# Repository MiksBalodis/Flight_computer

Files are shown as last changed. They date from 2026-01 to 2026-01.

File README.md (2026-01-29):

# Aktīvās kontroles raķetes avionikas sistēma

## Projekta apraksts
Šis projekts paredz aktīvās kontroles raķetes avionikas sistēmas izstrādi, kas ietver gan raķetē iebūvētu avionikas datoru, gan zemes bāzi datu saņemšanai, uzglabāšanai un analīzei. Sistēma nodrošina aktīvu trajektorijas korekciju reāllaikā, izmantojot sensoru datus, vadības algoritmus un elektroniskos izpildmehānismus.

Projektā tiek apvienotas iegultās sistēmas, signālu apstrāde, vadības algoritmi, telemetrija un lietotāja saskarnes izstrāde.

**Projektu izstrādā:**  
Aleksandrs Jesiļevskis  
Miks Balodis  

---

## Projekta mērķis
Izstrādāt:
- raķetes avionikas datoru ar aktīvas trajektorijas korekcijas iespējām,
- zemes bāzi lidojuma datu saņemšanai un analīzei,
- drošu un papildināmu sistēmu, kas piemērota eksperimentālām lieljaudas raķetēm.

Sistēmai jāspēj:
- reāllaikā noteikt raķetes stāvokli,
- veikt aktīvo vadību ar vairākām kontroles spurām,
- ierakstīt un uzglabāt lidojuma datus,
- nodrošināt saziņu ar zemes bāzi lidojuma laikā.

---

## Idejas rašanās
Ideja radās, balstoties uz **RTU Lieljaudas raķeškomandas (RTU HPR)** 2025. gada 1. semestra projektu – aktīvās rotācijas kontroles raķeti. Šī projekta ietvaros tika izmantots RP2040 mikrokontrolieris, kuram konstatēti vairāki ierobežojumi:
- nav iebūvēta peldošā komata vienības (FPU),
- ierobežota programmas atmiņa,
- augsts enerģijas patēriņš.

Lai šos trūkumus novērstu, projektā tiek izvēlēts **STM32F405RGT6**, kas nodrošina augstāku veiktspēju, FPU atbalstu un DSP instrukcijas.

---

## Idejas apraksts

### Projekta lietotāji
- studentu raķešu komandas,
- augstskolu/vidusskolu eksperimentēšanas grupas,
- iegulto sistēmu un vadības algoritmu izstrādātāji,
- eksperimentālu raķešu un bezpilota sistēmu entuziasti.

### Izmantotās tehnoloģijas
- **Iegultās sistēmas:** STM32 (ARM Cortex-M4)
- **Sensori:** barometrs, IMU, GNSS
- **Vadības algoritmi:** PID, Kalmana filtrs
- **Telemetrija:** sub-GHz radio sakari
- **Programmatūra:** C/C++, MatLab/Simulink (simulācijas), JavaScript un Svelte (GUI)
- **Projektēšana:** KiCad

### Piegādes formāts
Projekta rezultāts būs:
- raķetes avionikas sistēmas plate (PCB),
- iegultā programmatūra gatava demonstratīvam raķetes lidojumam (firmware),
- zemes bāzes programmatūra (GUI),
- dokumentācija.

Šāda pieeja ļauj sistēmu izmantot gan eksperimentālos lidojumos, gan simulācijās.

---

## Aktīvā kontrole
Aktīvā kontrole ir vadības sistēma, kas lidojuma laikā nepārtraukti:
- mēra raķetes stāvokli (leņķi, ātrumu, rotāciju),
- aprēķina nepieciešamos labojumus,
- ģenerē PWM signālus izpildmehānismiem servo kontrolētām spurām.

Sistēma atbalsta līdz **4 aktīvām spurām**, katrai paredzot atsevišķu PWM kanālu. Salīdzinājumā ar pasīvo kontroli, aktīvā kontrole spēj reaģēt uz ārējiem traucējumiem un uzlabot stabilitāti un precizitāti.

---

## Risinājuma arhitektūra

### Konceptuālais modelis
Sistēma sastāv no trim galvenajiem blokiem:
1. **Sensoru slānis** – datu iegūšana
2. **Vadības un apstrādes slānis** – aprēķini un lēmumu pieņemšana
3. **Izpildes un komunikācijas slānis** – kontrole, datu uzglabāšana un pārraide

### Tehniskā arhitektūra

#### MCU
- **STM32F405RGT6** - mikrokontrolieris datu apstrādei un komandu nodošanai

#### Sensori
- **BMP388** – barometrs augstuma noteikšanai
- **LSM6DSO** – IMU (akselerometrs + žiroskops)
- **MAX-M10S** – GNSS modulis augstas precizitātes pozīcijai

#### Datu uzglabāšana
- **MXL1606** – lidojuma datu ierakstīšanai (USB Mass Storage režīms)
- **24LC64 EEPROM** – konfigurācijas datiem

#### Telemetrija
- **EBYTE E22-400M22S** - LoRa moudlis saziņai ar zemes bāzi (433 MHz)

#### Vadība
- PWM signāli spuru servo
- PID regulators
- Kalmana filtrs stāvokļa novērtēšanai

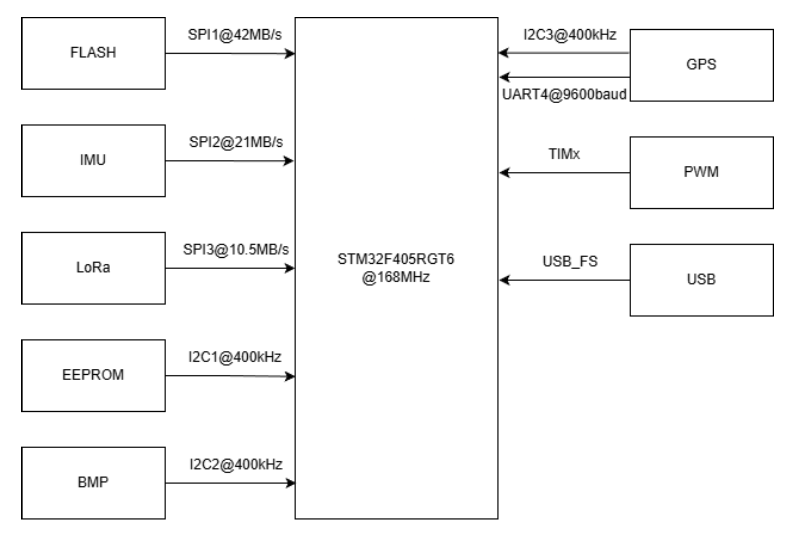
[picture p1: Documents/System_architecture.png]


---
## Izstrādes plāns (10 nedēļas)

Projekta izstrāde ir plānota 10 nedēļu laikā, pieņemot, ka avionikas plate jau ir uzdizainēta un pasūtīta, un nākamais solis ir tās salodēšana. Darbs tiek sadalīts starp diviem izstrādātājiem, lai maksimāli efektīvi izmantotu paralēlu izstrādi.

### Lomu sadalījums
- **Aleksandrs** – iegultās sistēmas programmēšana, STM32 firmware, sensoru draiveri, datu plūsma, vadība un telemetrija, sistēmas arhitektūras lēmumi,  integrācija, testēšana un dokumentācija.
- **Miks** – raķetes tehniskā daļa, mehāniskā integrācija, Matlab/Simulink simulācijas, vadības algoritmu modelēšana un zemes stacijas aparatūra, sistēmas arhitektūras lēmumi,  integrācija, testēšana un dokumentācija.

---

### 1. nedēļa – Sistēmas inicializācija un modeļu sagatavošana
**Aleksandrs:**
- STM32CubeIDE projekta izveide
- Pulksteņu (clock tree) un pamata perifēriju konfigurācija
- Debug interfeisa (SWD/UART) inicializācija

**Miks:**
- Raķetes kustības konceptuālā modeļa izstrāde
- Aktīvās kontroles uzdevuma definēšana
- Sensoru mērījumu teorētisko modeļu izveide

**Rezultāts:**  
MCU veiksmīgi startē un sistēmas matemātiskais modelis ir definēts.

---

### 2. nedēļa – Perifēriju un datu plūsmas pamati
**Aleksandrs:**
- GPIO, UART, SPI un I2C konfigurācija
- DMA izmantošanas pamati datu pārsūtīšanai
- Vienkārša datu izvada testēšana

**Miks:**
- PID regulatora struktūras izveide Matlab/Simulink
- Sākotnējo vadības parametru novērtēšana
- Avionikas plates salodēšana

**Rezultāts:**  
MCU spēj komunicēt ar perifērijām, un PID struktūra ir gatava simulācijām, plate ir salodēta.

---

### 3. nedēļa – Avionikas plates salodēšana un sensoru testēšana
**Aleksandrs:**
- IMU (LSM6DSO) un barometra (BMP388) draiveru izstrāde
- Sensoru datu nolasīšana un izvadīšana caur UART

**Miks:**
- Barošanas un signālu līmeņu pārbaude
- Sensoru fiziskās integrācijas novērtēšana

**Rezultāts:**  
Pilnībā funkcionējoši aktīvie sensori.

---

### 4. nedēļa – GNSS un sensoru apvienošana
**Aleksandrs:**
- GNSS (MAX-M10S) draivera izstrāde
- Laika sinhronizācija starp sensoriem
- Datu struktūru definēšana

**Miks:**
- Sensoru kalibrācijas metodes
- Kļūdu modelēšana
- Mērījumu precizitātes izvērtēšana

**Rezultāts:**  
Apvienoti visi sensoru dati vienotā laika skalā.

---

### 5. nedēļa – Aktīvā vadība un izpildmehānismi
**Aleksandrs:**
- PWM izvades konfigurācija
- Taimeru konfigurācija izpildmehānismiem
- Izpildmehānismu testēšana

**Miks:**
- PID parametru regulēšana Simulink vidē
- Stabilitātes analīze
- Vadības algoritma validācija simulācijā

**Rezultāts:**  
Izpildmehānismi reaģē uz vadības signāliem paredzētajā veidā.

---

### 6. nedēļa – Datu apstrāde un uzglabāšana
**Aleksandrs:**
- USB Mass Storage režīma ieviešana
- Datu struktūras optimizācija

**Miks:**
- Kalmana filtra izstrāde Simulink vidē
- Algoritma sagatavošana ieviešanai C kodā

**Rezultāts:**  
Stabili ierakstīti un izgūstami lidojuma dati.

---

### 7. nedēļa – Telemetrija un zemes stacijas aparatūra
**Aleksandrs:**
- Telemetrijas protokola izstrāde
- EBYTE E22 radio moduļa integrācija
- Datu pakešu formāta definēšana

**Miks:**
- Zemes stacijas plates arhitektūras izstrāde
- Komponentu izvēle un shēmas dizains
- Komunikācijas interfeisa plānošana

**Rezultāts:**  
Bezvadu datu pārraide starp raķeti un zemes staciju.

---

### 8. nedēļa – Zemes stacijas programmatūra un GUI
**Aleksandrs:**
- Seriālās komunikācijas protokols ar datoru
- Telemetrijas datu parsēšana

**Miks:**
- Grafiskās lietotāja saskarnes izstrāde (Svelte)
- Reāllaika grafiki un datu attēlošana
- Datu eksportēšana analīzei

**Rezultāts:**  
Darbojoša zemes stacija ar reāllaika datu vizualizāciju.

---

### 9. nedēļa – Integrācija un sistēmas testi
**Aleksandrs:**
- Pilna vadības cikla integrācija
- Kļūdu apstrāde un drošības mehānismi

**Miks:**
- Vibrāciju testi
- Sensoru trokšņu ietekmes pārbaude

**Rezultāts:**  
Stabila un integrēta sistēma bez kritiskām kļūdām.

---

### 10. nedēļa – Stabilizācija un dokumentācija
**Abi:**
- Koda un aparatūras kļūdu labošana
- Projekta dokumentācijas pabeigšana
- Demonstrācijas sagatavošana

**Rezultāts:**  
Pilnībā sagatavots projekts demonstrācijai un prezentācijai.

---

## Projekta izstrādes grafiks

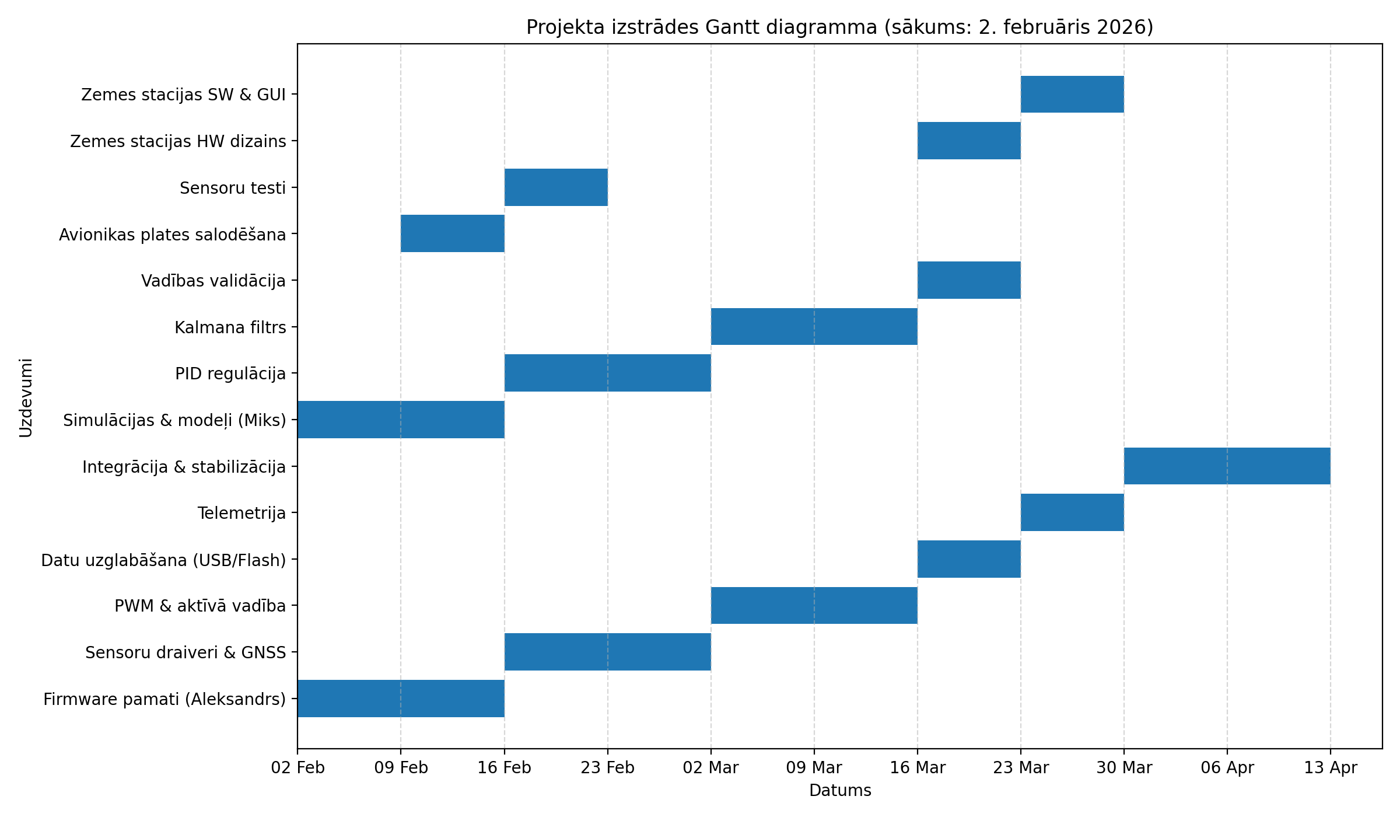
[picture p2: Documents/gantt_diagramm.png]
Projekta izstrādes Gantt diagramma


---

## Licence
Licence tiks noteikta projekta vēlākā izstrādes posmā.

---

## Kontakti
Jautājumu vai sadarbības gadījumā sazināties ar projekta izstrādātājiem.

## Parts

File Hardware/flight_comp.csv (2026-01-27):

Reference | Qty | Value | DNP | Exclude from BOM | Exclude from Board | Footprint | Datasheet
BT1 | 1 | MC621 |  |  |  | Battery:BatteryHolder_Keystone_2998_1x6.8mm | ~
BZ1 | 1 | Buzzer |  |  |  | Buzzer_Beeper:Buzzer_CUI_CPT-9019S-SMT | ~
C1,C2,C3,C34,C37,C41 | 6 | 100nF |  |  |  | Capacitor_SMD:C_0402_1005Metric | ~
C4 | 1 | 10µF |  |  |  | Capacitor_SMD:C_0402_1005Metric | ~
C5 | 1 | 47 µF |  |  |  | Capacitor_SMD:C_1206_3216Metric | ~
C6,C7 | 2 | 2.2uF |  |  |  | Capacitor_SMD:C_0603_1608Metric | ~
C8,C9 | 2 | 22pF |  |  |  | Capacitor_SMD:C_0603_1608Metric | ~
C10,C11,C14,C26,C27,C28,C29,C30,C31,C32,C33 | 11 | 0.1uF |  |  |  | Capacitor_SMD:C_0603_1608Metric | ~
C12 | 1 | 6.8nF |  |  |  | Capacitor_SMD:C_0603_1608Metric | ~
C13 | 1 | 1uF |  |  |  | Capacitor_SMD:C_0603_1608Metric | ~
C15 | 1 | 44uF |  |  |  | Capacitor_SMD:C_0805_2012Metric | ~
C16 | 1 | 22uF |  |  |  | Capacitor_SMD:C_0805_2012Metric | ~
C17 | 1 | 100nF |  |  |  | Capacitor_SMD:C_0603_1608Metric | ~
C18,C42 | 2 | 10uF |  |  |  | Capacitor_SMD:C_0603_1608Metric | ~
C19 | 1 | 22uF |  |  |  | Capacitor_SMD:C_0603_1608Metric | ~
C20,C23 | 2 | 22pF |  |  |  | Capacitor_SMD:C_0402_1005Metric | ~
C21,C22 | 2 | 0.1uF |  |  |  | Capacitor_SMD:C_0402_1005Metric | ~
C24 | 1 | 6TPF470MFH |  |  |  | Capacitor_Tantalum_SMD:CP_EIA-3216-10_Kemet-I | https://industrial.panasonic.com/cdbs/www-data/pdf/AAA8000/AAA8000C38.pdf
C35,C36 | 2 | 10uF |  |  |  | Capacitor_SMD:C_0402_1005Metric | ~
D1 | 1 | LED |  |  |  | LED_SMD:LED_0603_1608Metric | ~
D2,D5 | 2 | D_TVS |  |  |  | Diode_SMD:D_SOD-523 | ~
D3 | 1 | SS24 |  |  |  | Diode_SMD:D_SMA | https://www.vishay.com/docs/88748/ss22.pdf
D4 | 1 | SK6812 |  |  |  | LED_SMD:LED_SK6812_PLCC4_5.0x5.0mm_P3.2mm | https://cdn-shop.adafruit.com/product-files/1138/SK6812+LED+datasheet+.pdf
D6 | 1 | 3.6V |  |  |  | Diode_SMD:D_SOD-128 | ~
E22-400M22S2 | 1 | ~ |  |  |  | E22-400M22S:E22-400M22S
F1 | 1 | Fuse |  |  |  | Fuse:Fuse_1206_3216Metric | ~
H1,H2,H3,H4 | 4 | MountingHole |  | Excluded from BOM |  | MountingHole:MountingHole_3.2mm_M3 | ~
IC1 | 1 | BMP388 |  |  |  | Package_LGA:ST_HLGA-10_2x2mm_P0.5mm_LayoutBorder3x2y | https://ae-bst.resource.bosch.com/media/_tech/media/datasheets/BST-BMP388-DS001.pdf
IC4 | 1 | TPS259531DSGR |  |  |  | Package_SON:WSON-8-1EP_2x2mm_P0.5mm_EP0.9x1.6mm_ThermalVias | http://www.ti.com/lit/gpn/tps2595
J1,J12 | 2 | Conn_Coaxial |  |  |  | Connector_Coaxial:SMA_Molex_73251-2200_Horizontal | ~
J2 | 1 | TC2030 |  | Excluded from BOM |  | Connector:Tag-Connect_TC2030-IDC-NL_2x03_P1.27mm_Vertical | https://www.tag-connect.com/wp-content/uploads/bsk-pdf-manager/2019/12/TC2030-IDC-NL-Datasheet-Rev-B.pdf
J3 | 1 | XT30 |  |  |  | Connector_AMASS:AMASS_XT30PW-M_1x02_P2.50mm_Horizontal | ~
J4 | 1 | USB_C_Receptacle_USB2.0_16P |  |  |  | Connector_USB:USB_C_Receptacle_GCT_USB4110 | https://www.usb.org/sites/default/files/documents/usb_type-c.zip
J5,J6 | 2 | Conn_01x02 |  |  |  | TerminalBlock_4Ucon:TerminalBlock_4Ucon_1x02_P3.50mm_Vertical | ~
J7 | 1 | SERVO_CONN_01 |  |  |  | Connector_PinHeader_2.54mm:PinHeader_2x03_P2.54mm_Vertical | ~
J8,J9 | 2 | SERVO_CONN_02 |  |  |  | Connector_PinHeader_2.54mm:PinHeader_2x03_P2.54mm_Vertical | ~
J10 | 1 | CAMERA_CONN_01 |  |  |  | TerminalBlock:TerminalBlock_Xinya_XY308-2.54-2P_1x02_P2.54mm_Horizontal | ~
J11 | 1 | CAMERA_CONN_02 |  |  |  | TerminalBlock:TerminalBlock_Xinya_XY308-2.54-2P_1x02_P2.54mm_Horizontal | ~
J13 | 1 | CAMERA_CONN_03 |  |  |  | TerminalBlock:TerminalBlock_Xinya_XY308-2.54-2P_1x02_P2.54mm_Horizontal | ~
L1 | 1 | 2.2uH |  |  |  | Inductor_SMD:L_6.3x6.3_H3 | ~
L2 | 1 | L |  |  |  | Inductor_SMD:L_0603_1608Metric | ~
Q2 | 1 | DMP3013SFV |  |  |  | Package_SON:Diodes_PowerDI3333-8 | https://www.diodes.com/assets/Datasheets/DMP3013SFV.pdf
Q3,Q4 | 2 | CSD17577Q3A |  |  |  | Package_SON:VSON-8_3.3x3.3mm_P0.65mm_NexFET | https://www.ti.com/lit/ds/symlink/csd17577q3a.pdf
Q5 | 1 | PMBT2222A |  |  |  | Package_TO_SOT_SMD:SOT-23 | https://assets.nexperia.com/documents/data-sheet/PMBT2222A.pdf
R1,R2,R3,R4 | 4 | 100Ω |  |  |  | Resistor_SMD:R_0402_1005Metric | ~
R5,R6,R7,R21 | 4 | 10k |  |  |  | Resistor_SMD:R_0603_1608Metric | ~
R8,R33 | 2 | 1k |  |  |  | Resistor_SMD:R_0603_1608Metric | ~
R9 | 1 | 604k |  |  |  | Resistor_SMD:R_0603_1608Metric | ~
R10 | 1 | 40.2k |  |  |  | Resistor_SMD:R_0603_1608Metric | ~
R11 | 1 | 13k |  |  |  | Resistor_SMD:R_0603_1608Metric | ~
R12 | 1 | 20k |  |  |  | Resistor_SMD:R_0603_1608Metric | ~
R13 | 1 | 20R |  |  |  | Resistor_SMD:R_0603_1608Metric | ~
R14 | 1 | 4.7k |  |  |  | Resistor_SMD:R_0603_1608Metric | ~
R15,R16 | 2 | 22R |  |  |  | Resistor_SMD:R_0603_1608Metric | ~
R17,R18,R19,R20,R22,R23 | 6 | 100 |  |  |  | Resistor_SMD:R_0402_1005Metric | ~
R24,R25,R26,R27,R28,R29 | 6 | R | DNP |  |  | Resistor_SMD:R_0603_1608Metric | ~
R30,R31 | 2 | R |  |  |  | Resistor_SMD:R_0603_1608Metric | ~
R32 | 1 | 0R | DNP |  |  | Resistor_SMD:R_0603_1608Metric | ~
R34 | 1 | 5k |  |  |  | Resistor_SMD:R_0402_1005Metric | ~
R48 | 1 | 220Ω |  |  |  | Resistor_SMD:R_0402_1005Metric | ~
SW1 | 1 | NRST |  |  |  | Button_Switch_SMD:SW_SPST_CK_RS282G05A3 | ~
SW2 | 1 | BOOT0 |  |  |  | Button_Switch_SMD:SW_SPST_CK_RS282G05A3 | ~
SW3 | 1 | EG2219 |  |  |  | Button_Switch_SMD:SW_DPDT_CK_JS202011JCQN | ~
TX4 | 1 | XL-1608UBC-04 |  |  |  | LED_SMD:LED_0603_1608Metric | https://fscdn.rohm.com/en/products/databook/datasheet/discrete/diode/switching/1ss355vmte-17-e.pdf
U1 | 1 | STM32F405RGTx |  |  |  | Package_QFP:LQFP-64_10x10mm_P0.5mm | https://www.st.com/resource/en/datasheet/stm32f405rg.pdf
U2 | 1 | MAX-M10S |  |  |  | RF_GPS:ublox_MAX | https://content.u-blox.com/sites/default/files/MAX-M10S_DataSheet_UBX-20035208.pdf
U3 | 1 | 74LVC1GU04 |  |  |  | Package_TO_SOT_SMD:SOT-23-5 | http://www.ti.com/lit/sg/scyt129e/scyt129e.pdf
U4 | 1 | W25Q32JVSS |  |  |  | Package_SO:SOIC-8_5.3x5.3mm_P1.27mm | http://www.winbond.com/resource-files/w25q32jv%20revg%2003272018%20plus.pdf
U5 | 1 | 24LC64 |  |  |  | Package_TO_SOT_SMD:SOT-23-5 | http://ww1.microchip.com/downloads/en/DeviceDoc/21189f.pdf
U6 | 1 | MP2331 |  |  |  | Package_TO_SOT_SMD:SOT-583-8
U7 | 1 | AMS1117-5.0 |  |  |  | Package_TO_SOT_SMD:SOT-223-3_TabPin2 | http://www.advanced-monolithic.com/pdf/ds1117.pdf
U8 | 1 | USBLC6-2SC6 |  |  |  | Package_TO_SOT_SMD:SOT-23-6 | https://www.st.com/resource/en/datasheet/usblc6-2.pdf
U10 | 1 | LTC4412 |  |  |  | Package_TO_SOT_SMD:TSOT-23-6 | https://www.analog.com/media/en/technical-documentation/data-sheets/4412fb.pdf
U11,U12 | 2 | UCC27517A |  |  |  | Package_TO_SOT_SMD:SOT-23-5 | https://www.ti.com/lit/ds/symlink/ucc27517a.pdf
U13 | 1 | LSM6DSO |  |  |  | Package_LGA:LGA-14_3x2.5mm_P0.5mm_LayoutBorder3x4y
Y1 | 1 | 8mHz |  |  |  | Crystal:Crystal_SMD_5032-2Pin_5.0x3.2mm | ~
Y2 | 1 | 32.768 kHz |  |  |  | Crystal:Crystal_SMD_3215-2Pin_3.2x1.5mm | ~

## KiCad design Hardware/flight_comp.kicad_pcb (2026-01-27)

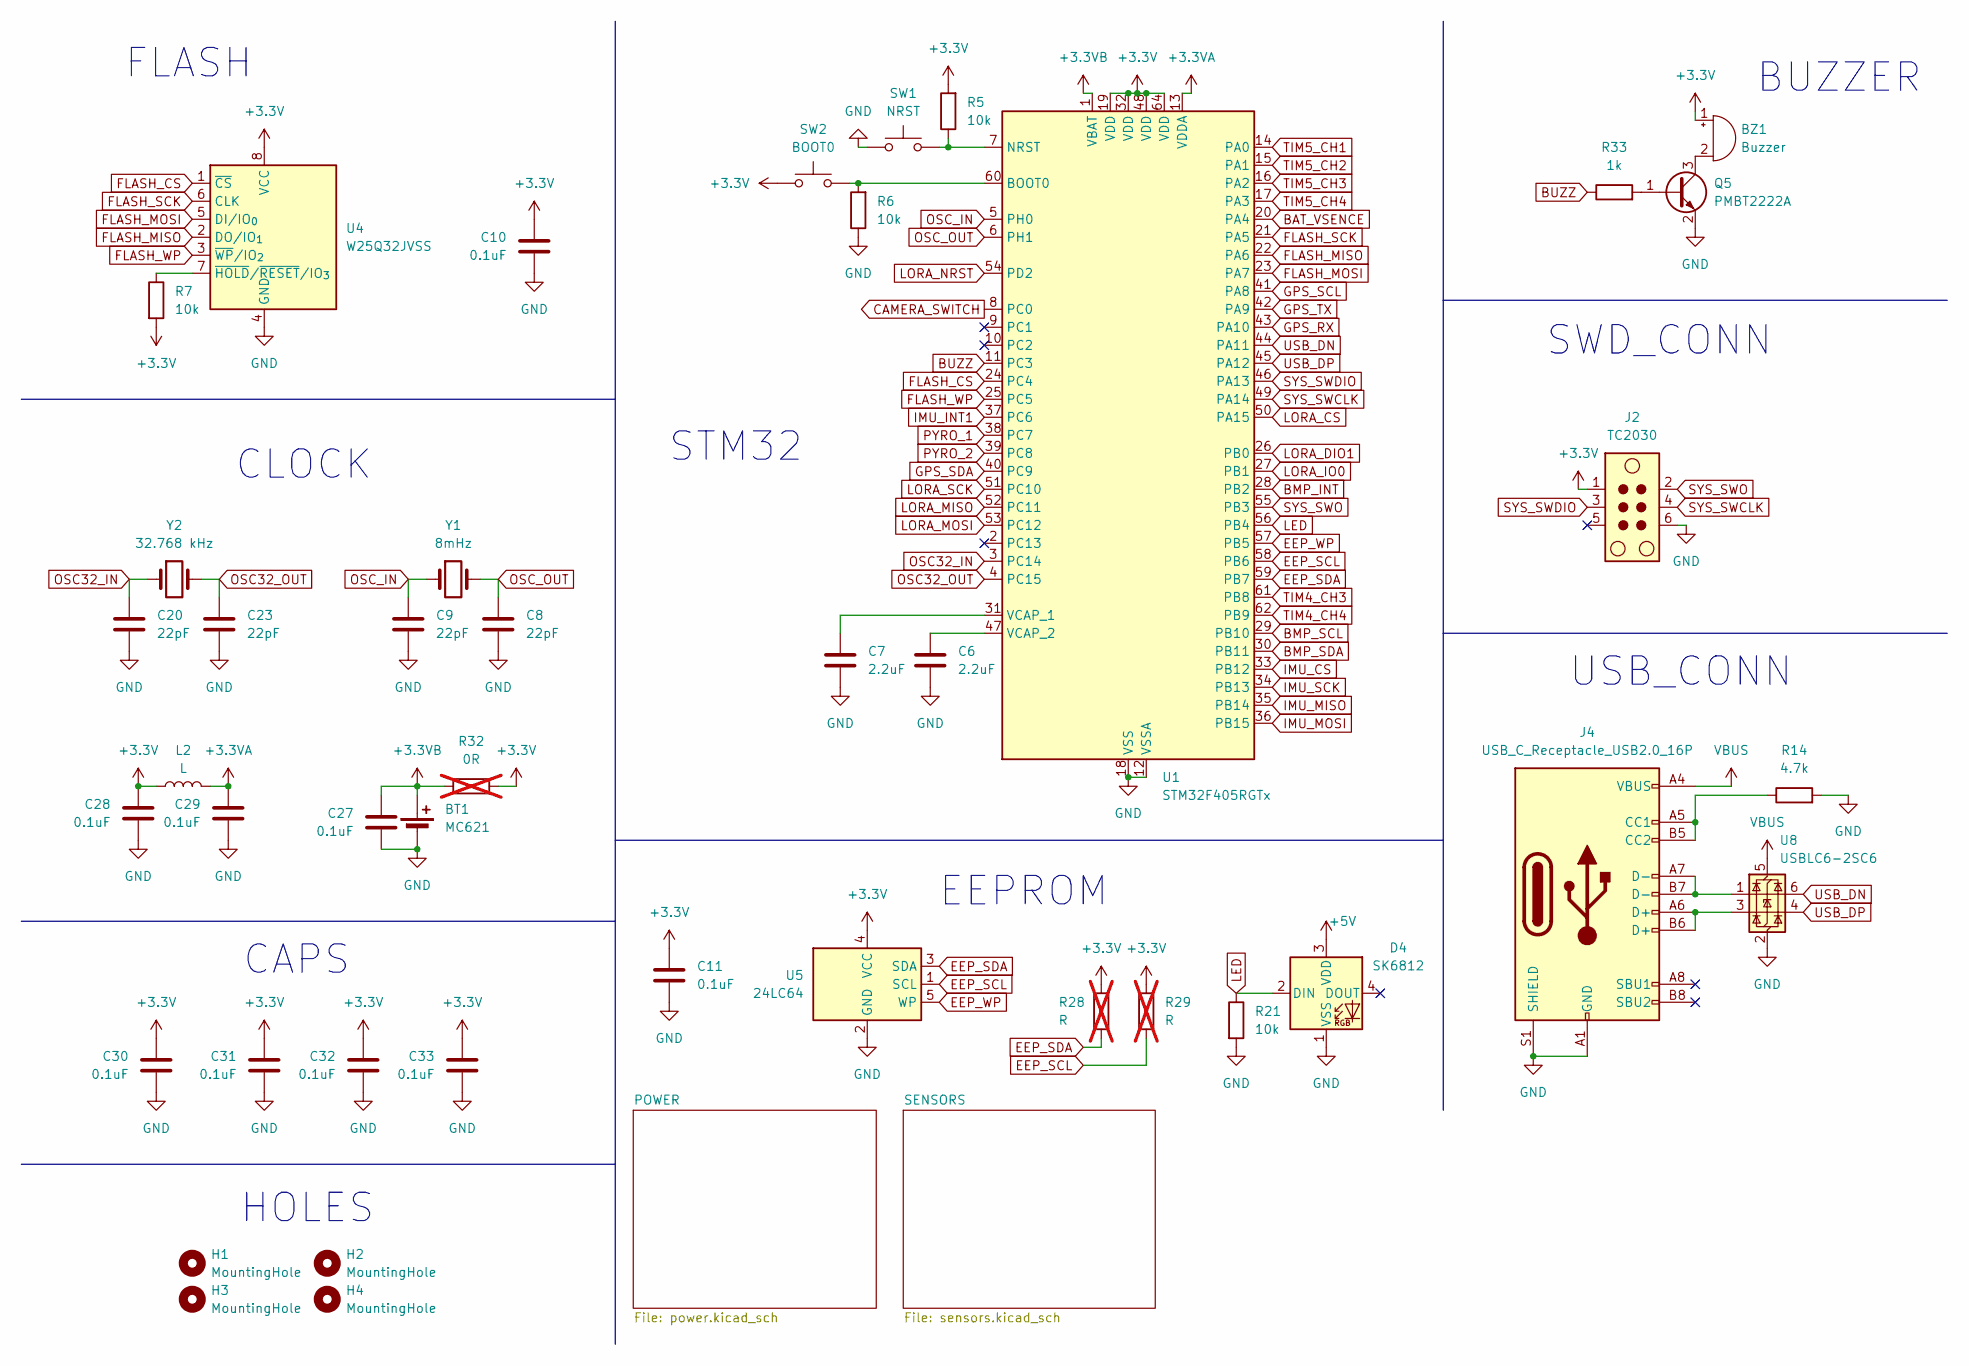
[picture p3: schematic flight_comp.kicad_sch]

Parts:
BT1: MC621; BatteryHolder_Keystone_2998_1x6.8mm
BZ1: Buzzer; Buzzer_CUI_CPT-9019S-SMT
C6, C7: 2.2uF; C_0603_1608Metric
C8, C9: 22pF; C_0603_1608Metric
C10, C11, C27, C28, C29, C30, C31, C32, C33: 0.1uF; C_0603_1608Metric
C20, C23: 22pF; C_0402_1005Metric
D4: SK6812; LED_SK6812_PLCC4_5.0x5.0mm_P3.2mm
H1, H2, H3, H4: MountingHole; MountingHole_3.2mm_M3
J2: TC2030; Tag-Connect_TC2030-IDC-NL_2x03_P1.27mm_Vertical
J4: USB_C_Receptacle_USB2.0_16P; USB_C_Receptacle_GCT_USB4110
L2: L; L_0603_1608Metric
Q5: PMBT2222A; SOT-23
R5, R6, R7, R21: 10k; R_0603_1608Metric
R14: 4.7k; R_0603_1608Metric
R28, R29: R; R_0603_1608Metric; not fitted
R32: 0R; R_0603_1608Metric; not fitted
R33: 1k; R_0603_1608Metric
SW1: NRST; SW_SPST_CK_RS282G05A3
SW2: BOOT0; SW_SPST_CK_RS282G05A3
U1: STM32F405RGTx; LQFP-64_10x10mm_P0.5mm
U4: W25Q32JVSS; SOIC-8_5.3x5.3mm_P1.27mm
U5: 24LC64; SOT-23-5
U8: USBLC6-2SC6; SOT-23-6
Y1: 8mHz; Crystal_SMD_5032-2Pin_5.0x3.2mm
Y2: 32.768 kHz; Crystal_SMD_3215-2Pin_3.2x1.5mm

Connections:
+3.3V: BZ1.1 (+), C10.1, C11.1, C28.1, C30.1, C31.1, C32.1, C33.1, J2.1, L2.1, R5.2, R7.2, R28.1, R29.1, R32.2, SW2.1, U1.19 (VDD), U1.32 (VDD), U1.48 (VDD), U1.64 (VDD), U4.8 (VCC), U5.4 (VCC); also elsewhere on the board
+3.3VA: C29.1, L2.2, U1.13 (VDDA)
+3.3VB: BT1.1 (+), C27.1, R32.1, U1.1 (VBAT)
+5V: D4.3 (VDD); also elsewhere on the board
BAT_VSENCE: U1.20 (PA4); also elsewhere on the board
BMP_INT: U1.28 (PB2); also elsewhere on the board
BMP_SCL: U1.29 (PB10); also elsewhere on the board
BMP_SDA: U1.30 (PB11); also elsewhere on the board
BUZZ: R33.1, U1.11 (PC3)
CAMERA_SWITCH: U1.8 (PC0); also elsewhere on the board
EEP_SCL: R29.2, U1.58 (PB6), U5.1 (SCL)
EEP_SDA: R28.2, U1.59 (PB7), U5.3 (SDA)
EEP_WP: U1.57 (PB5), U5.5 (WP)
FLASH_CS: U1.24 (PC4), U4.1 (~CS)
FLASH_MISO: U1.22 (PA6), U4.2 (DO/IO_{1})
FLASH_MOSI: U1.23 (PA7), U4.5 (DI/IO_{0})
FLASH_SCK: U1.21 (PA5), U4.6 (CLK)
FLASH_WP: U1.25 (PC5), U4.3 (~WP/IO_{2})
GND: BT1.2 (-), C6.2, C7.2, C8.2, C9.2, C10.2, C11.2, C20.2, C23.2, C27.2, C28.2, C29.2, C30.2, C31.2, C32.2, C33.2, D4.1 (VSS), J2.6, J4.A1 (GND), J4.A12 (GND), J4.B1 (GND), J4.B12 (GND), J4.S1 (SHIELD), Q5.2 (E), R6.1, R14.2, R21.2, SW1.1, U1.12 (VSSA), U1.18 (VSS), U1.63 (VSS), U4.4 (GND), U5.2 (GND), U8.2 (GND); also elsewhere on the board
GPS_RX: U1.43 (PA10); also elsewhere on the board
GPS_SCL: U1.41 (PA8); also elsewhere on the board
GPS_SDA: U1.40 (PC9); also elsewhere on the board
GPS_TX: U1.42 (PA9); also elsewhere on the board
IMU_CS: U1.33 (PB12); also elsewhere on the board
IMU_INT1: U1.37 (PC6); also elsewhere on the board
IMU_MISO: U1.35 (PB14); also elsewhere on the board
IMU_MOSI: U1.36 (PB15); also elsewhere on the board
IMU_SCK: U1.34 (PB13); also elsewhere on the board
LED: D4.2 (DIN), R21.1, U1.56 (PB4)
LORA_CS: U1.50 (PA15); also elsewhere on the board
LORA_DIO1: U1.26 (PB0); also elsewhere on the board
LORA_IO0: U1.27 (PB1); also elsewhere on the board
LORA_MISO: U1.52 (PC11); also elsewhere on the board
LORA_MOSI: U1.53 (PC12); also elsewhere on the board
LORA_NRST: U1.54 (PD2); also elsewhere on the board
LORA_SCK: U1.51 (PC10); also elsewhere on the board
unnamed: BZ1.2 (-), Q5.3 (C)
unnamed: J4.A5 (CC1), J4.B5 (CC2), R14.1
unnamed: J4.A6 (D+), J4.B6 (D+), U8.3 (I/O2)
unnamed: J4.A7 (D-), J4.B7 (D-), U8.1 (I/O1)
unnamed: Q5.1 (B), R33.2
unnamed: R6.2, SW2.2, U1.60 (BOOT0)
unnamed: R5.1, SW1.2, U1.7 (NRST)
unnamed: C7.1, U1.31 (VCAP_1)
unnamed: C6.1, U1.47 (VCAP_2)
unnamed: R7.1, U4.7 (~HOLD/~RESET/IO_{3})
OSC32_IN: C20.1, U1.3 (PC14), Y2.1
OSC32_OUT: C23.1, U1.4 (PC15), Y2.2
OSC_IN: C9.1, U1.5 (PH0), Y1.1
OSC_OUT: C8.1, U1.6 (PH1), Y1.2
PYRO_1: U1.38 (PC7); also elsewhere on the board
PYRO_2: U1.39 (PC8); also elsewhere on the board
SYS_SWCLK: J2.4, U1.49 (PA14)
SYS_SWDIO: J2.3, U1.46 (PA13)
SYS_SWO: J2.2, U1.55 (PB3)
TIM4_CH3: U1.61 (PB8); also elsewhere on the board
TIM4_CH4: U1.62 (PB9); also elsewhere on the board
TIM5_CH1: U1.14 (PA0); also elsewhere on the board
TIM5_CH2: U1.15 (PA1); also elsewhere on the board
TIM5_CH3: U1.16 (PA2); also elsewhere on the board
TIM5_CH4: U1.17 (PA3); also elsewhere on the board
USB_DN: U1.44 (PA11), U8.6 (I/O1)
USB_DP: U1.45 (PA12), U8.4 (I/O2)
VBUS: J4.A4 (VBUS), J4.A9 (VBUS), J4.B4 (VBUS), J4.B9 (VBUS), U8.5 (VBUS); also elsewhere on the board

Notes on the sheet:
CAPS
CLOCK
BUZZER
USB_CONN
EEPROM
STM32
SWD_CONN
HOLES
FLASH

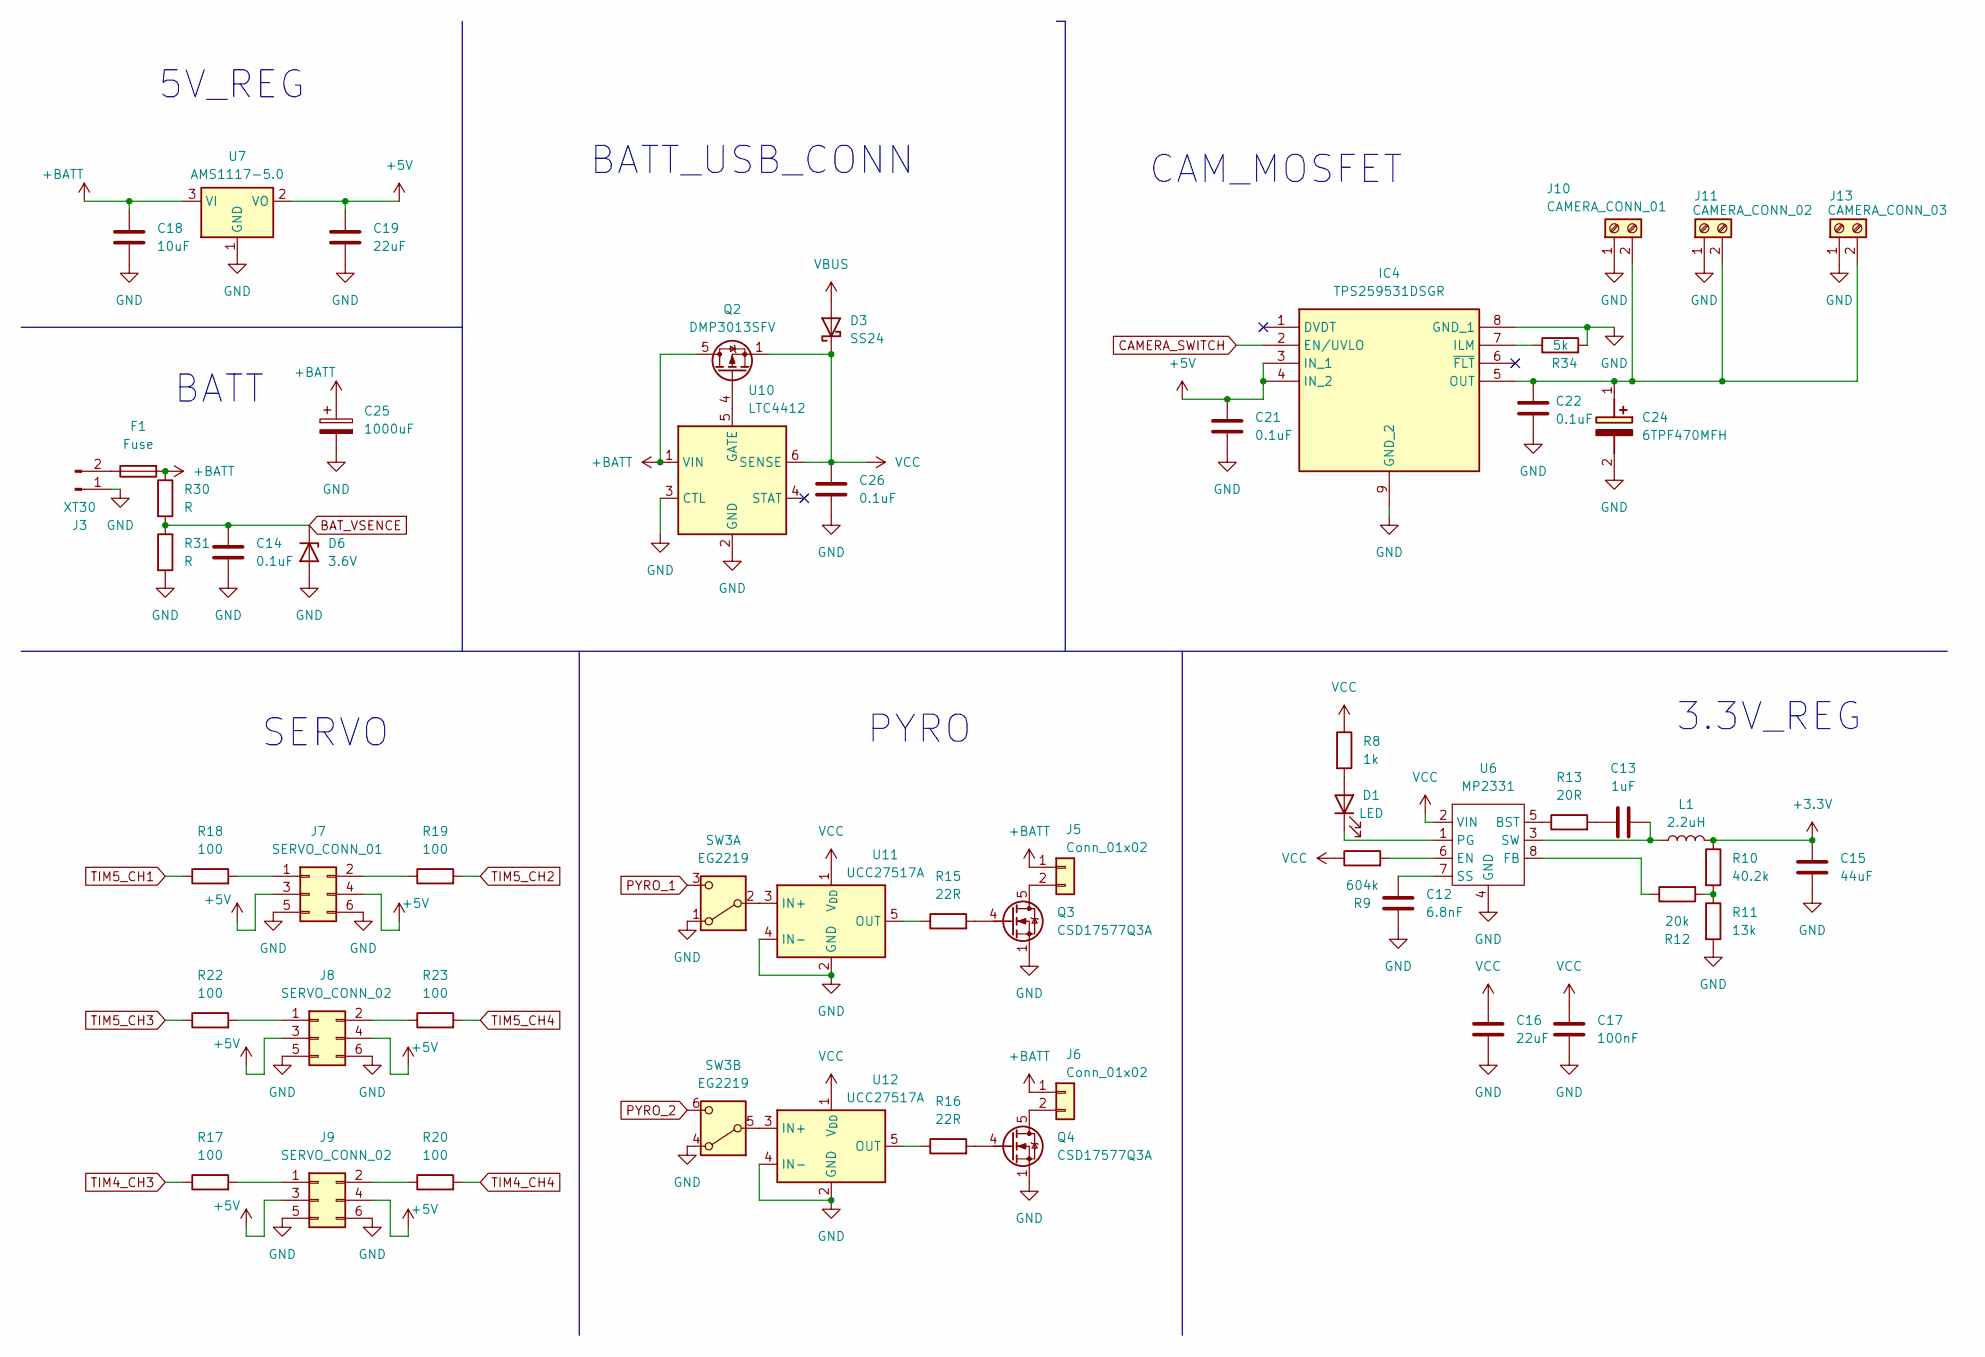
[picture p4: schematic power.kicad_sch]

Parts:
C12: 6.8nF; C_0603_1608Metric
C13: 1uF; C_0603_1608Metric
C14, C26: 0.1uF; C_0603_1608Metric
C15: 44uF; C_0805_2012Metric
C16: 22uF; C_0805_2012Metric
C17: 100nF; C_0603_1608Metric
C18: 10uF; C_0603_1608Metric
C19: 22uF; C_0603_1608Metric
C21, C22: 0.1uF; C_0402_1005Metric; MPN C0402C104K4RAC7411
C24: 6TPF470MFH; CP_EIA-3216-10_Kemet-I; Mouser Part Number 667-6TPF470MFH
C25: 1000uF; CP_Axial_L10.0mm_D6.0mm_P15.00mm_Horizontal
D1: LED; LED_0603_1608Metric
D3: SS24; D_SMA
D6: 3.6V; D_SOD-128
F1: Fuse; Fuse_1206_3216Metric
IC4: TPS259531DSGR; WSON-8-1EP_2x2mm_P0.5mm_EP0.9x1.6mm_ThermalVias; Mouser Part Number 595-TPS259531DSGR
J3: XT30; AMASS_XT30PW-M_1x02_P2.50mm_Horizontal
J5, J6: Conn_01x02; TerminalBlock_4Ucon_1x02_P3.50mm_Vertical; MPN 284514-2
J7: SERVO_CONN_01; PinHeader_2x03_P2.54mm_Vertical; MPN 90131-0763
J8, J9: SERVO_CONN_02; PinHeader_2x03_P2.54mm_Vertical; MPN 90131-0763
J10: CAMERA_CONN_01; TerminalBlock_Xinya_XY308-2.54-2P_1x02_P2.54mm_Horizontal; MPN 284514-2
J11: CAMERA_CONN_02; TerminalBlock_Xinya_XY308-2.54-2P_1x02_P2.54mm_Horizontal; MPN 284514-2
J13: CAMERA_CONN_03; TerminalBlock_Xinya_XY308-2.54-2P_1x02_P2.54mm_Horizontal; MPN 284514-2
L1: 2.2uH; L_6.3x6.3_H3
Q2: DMP3013SFV; Diodes_PowerDI3333-8
Q3, Q4: CSD17577Q3A; VSON-8_3.3x3.3mm_P0.65mm_NexFET
R8: 1k; R_0603_1608Metric
R9: 604k; R_0603_1608Metric
R10: 40.2k; R_0603_1608Metric
R11: 13k; R_0603_1608Metric
R12: 20k; R_0603_1608Metric
R13: 20R; R_0603_1608Metric
R15, R16: 22R; R_0603_1608Metric
R17, R19, R20, R22, R23: 100; R_0402_1005Metric; MPN RC1206FR-07100RL
R18: 100; R_0402_1005Metric
R30, R31: R; R_0603_1608Metric
R34: 5k; R_0402_1005Metric; MPN RC0402FR-075K76L
SW3: EG2219; SW_DPDT_CK_JS202011JCQN
U6: MP2331; SOT-583-8
U7: AMS1117-5.0; SOT-223-3_TabPin2
U10: LTC4412; TSOT-23-6
U11, U12: UCC27517A; SOT-23-5

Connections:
+3.3V: C15.1, L1.2, R10.1; also elsewhere on the board
+5V: C19.1, C21.1, IC4.3 (IN_1), IC4.4 (IN_2), J7.3, J7.4, J8.3, J8.4, J9.3, J9.4, U7.2 (VO); also elsewhere on the board
+BATT: C18.1, C25.1, F1.2, J5.1, J6.1, Q2.5 (D), R30.1, U7.3 (VI), U10.1 (VIN)
BAT_VSENCE: C14.1, D6.1 (K), R30.2, R31.1; also elsewhere on the board
CAMERA_SWITCH: IC4.2 (EN/UVLO); also elsewhere on the board
GND: C12.2, C14.2, C15.2, C16.2, C17.2, C18.2, C19.2, C21.2, C22.2, C24.2 (-), C25.2, C26.2, D6.2 (A), IC4.8 (GND_1), IC4.9 (GND_2), J3.1, J7.5, J7.6, J8.5, J8.6, J9.5, J9.6, J10.1, J11.1, J13.1, Q3.1 (S), Q3.2 (S), Q3.3 (S), Q4.1 (S), Q4.2 (S), Q4.3 (S), R11.2, R31.2, R34.2, SW3.1 (A), SW3.4 (A), U6.4 (GND), U7.1 (GND), U10.2 (GND), U10.3 (CTL), U11.2 (GND), U11.4 (IN-), U12.2 (GND), U12.4 (IN-); also elsewhere on the board
unnamed: C13.1, R13.2
unnamed: C22.1, C24.1 (+), IC4.5 (OUT), J10.2, J11.2, J13.2
unnamed: D1.2 (A), R8.2
unnamed: D1.1 (K), U6.1 (PG)
unnamed: IC4.7 (ILM), R34.1
unnamed: F1.1, J3.2
unnamed: J5.2, Q3.5 (D)
unnamed: J6.2, Q4.5 (D)
unnamed: J7.1, R18.2
unnamed: J7.2, R19.1
unnamed: J8.1, R22.2
unnamed: J8.2, R23.1
unnamed: J9.1, R17.2
unnamed: J9.2, R20.1
unnamed: Q2.4 (G), U10.5 (GATE)
unnamed: Q3.4 (G), R15.2
unnamed: Q4.4 (G), R16.2
unnamed: R10.2, R11.1, R12.2
unnamed: SW3.2 (B), U11.3 (IN+)
unnamed: SW3.5 (B), U12.3 (IN+)
unnamed: R13.1, U6.5 (BST)
unnamed: R9.2, U6.6 (EN)
unnamed: R12.1, U6.8 (FB)
unnamed: C12.1, U6.7 (SS)
unnamed: C13.2, L1.1, U6.3 (SW)
unnamed: R15.1, U11.5 (OUT)
unnamed: R16.1, U12.5 (OUT)
PYRO_1: SW3.3 (C); also elsewhere on the board
PYRO_2: SW3.6 (C); also elsewhere on the board
TIM4_CH3: R17.1; also elsewhere on the board
TIM4_CH4: R20.2; also elsewhere on the board
TIM5_CH1: R18.1; also elsewhere on the board
TIM5_CH2: R19.2; also elsewhere on the board
TIM5_CH3: R22.1; also elsewhere on the board
TIM5_CH4: R23.2; also elsewhere on the board
VBUS: D3.2 (A); also elsewhere on the board
VCC: C16.1, C17.1, C26.1, D3.1 (K), Q2.1 (S), Q2.2 (S), Q2.3 (S), R8.1, R9.1, U6.2 (VIN), U10.6 (SENSE), U11.1 (V_{DD}), U12.1 (V_{DD})

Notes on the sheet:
SERVO
PYRO
BATT_USB_CONN
5V_REG
3.3V_REG
BATT
CAM_MOSFET

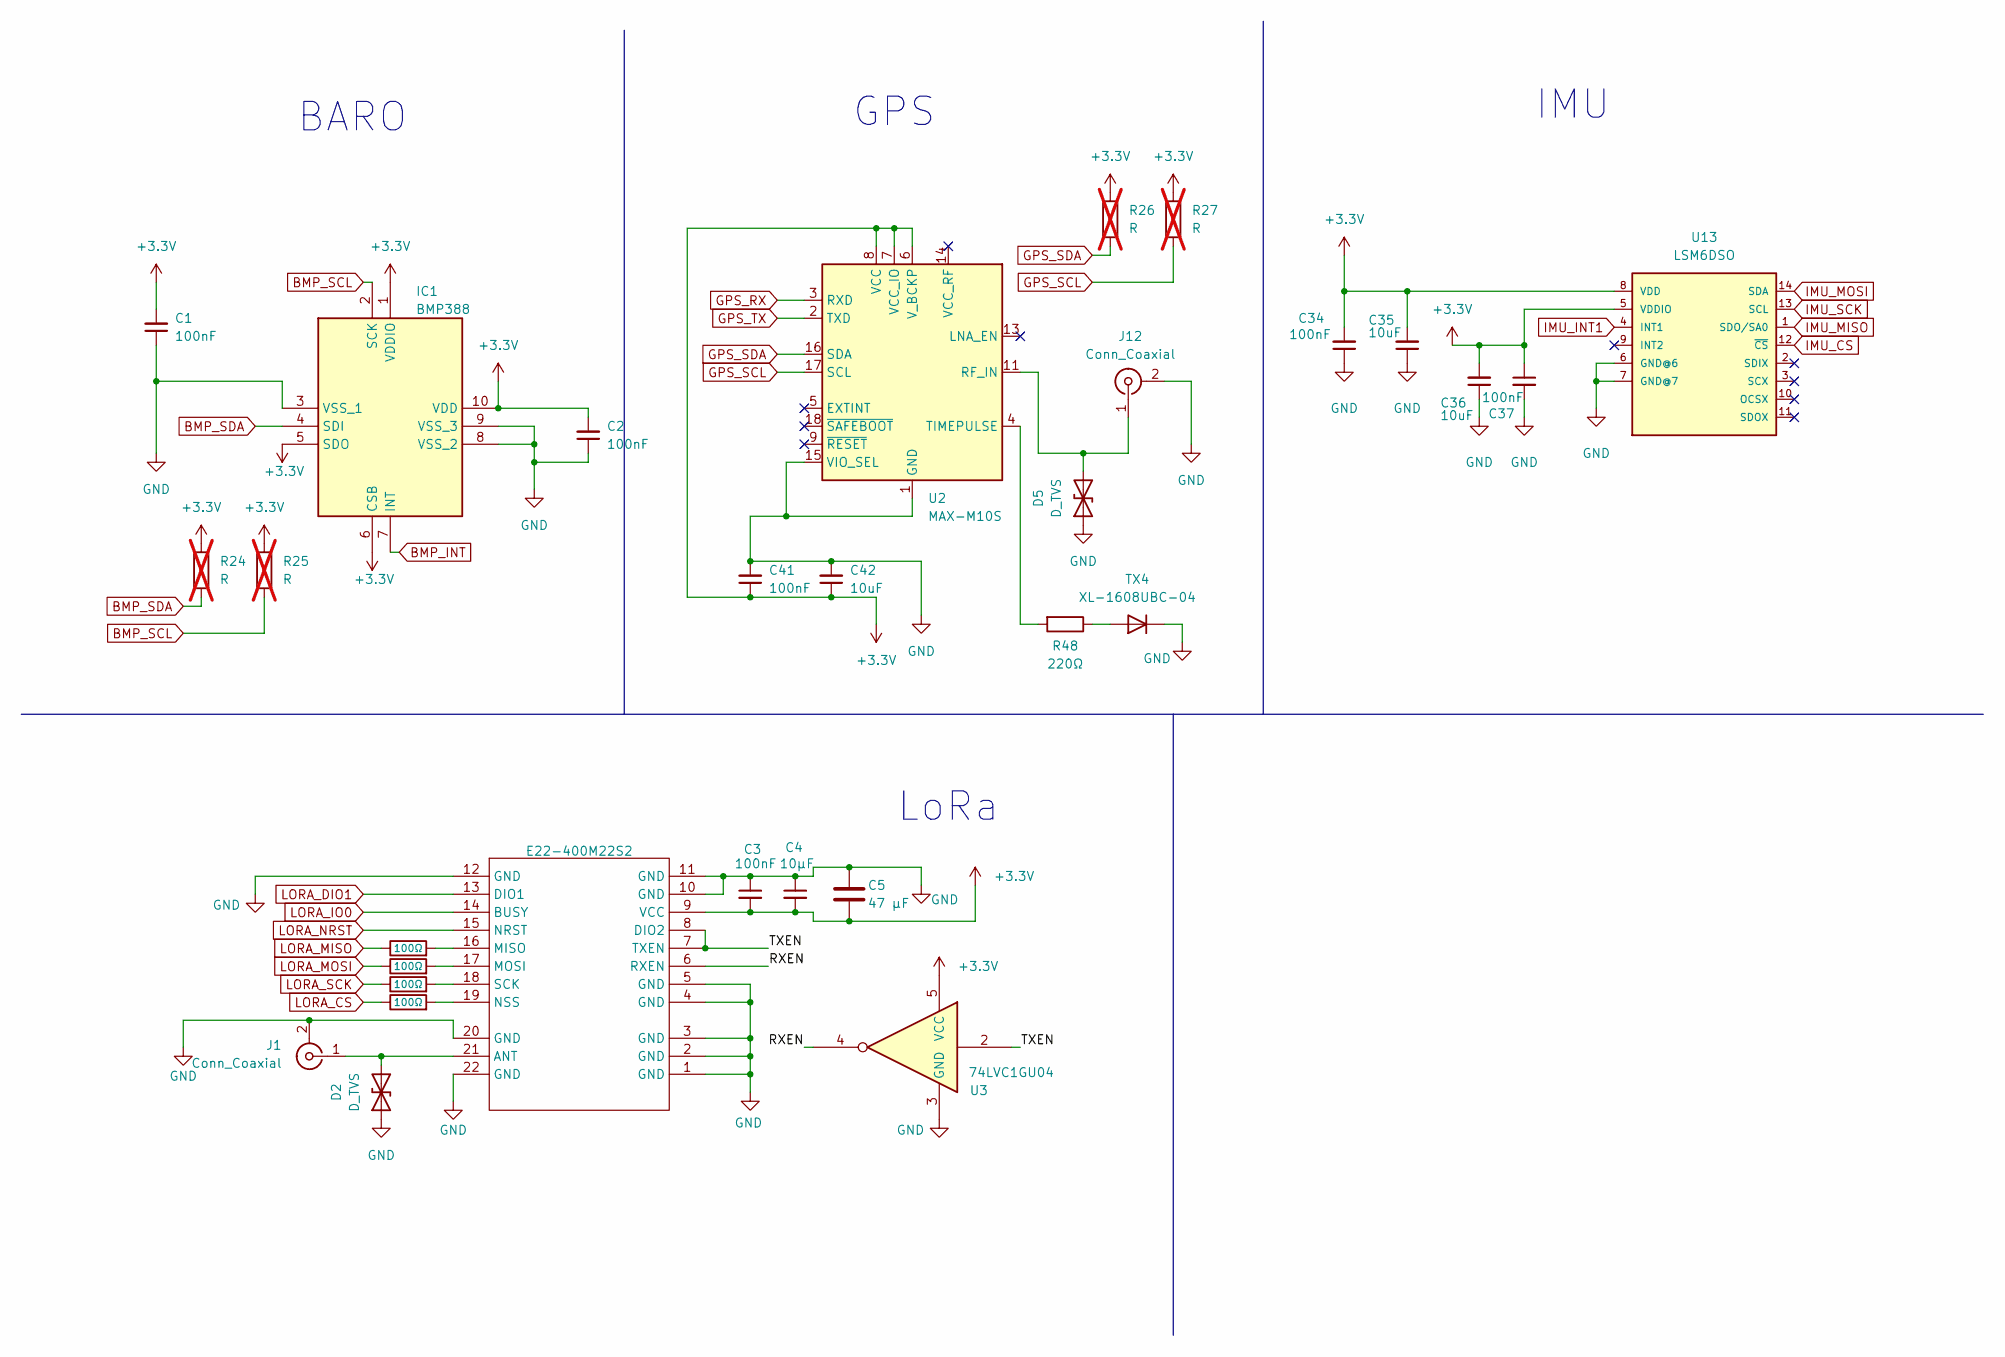
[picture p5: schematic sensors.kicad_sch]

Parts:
C1, C2, C3, C41: 100nF; C_0402_1005Metric
C4: 10µF; C_0402_1005Metric
C5: 47 µF; C_1206_3216Metric
C34, C37: 100nF; C_0402_1005Metric; MPN C0402C104K4RAC7411
C35, C36: 10uF; C_0402_1005Metric; MPN C0402C106M9PACTU
C42: 10uF; C_0603_1608Metric
D2, D5: D_TVS; D_SOD-523
E22-400M22S2: E22-400M22S
IC1: BMP388; ST_HLGA-10_2x2mm_P0.5mm_LayoutBorder3x2y; Manufacturer_Part_Number BMP388
J1, J12: Conn_Coaxial; SMA_Molex_73251-2200_Horizontal
R1, R2, R3, R4: 100Ω; R_0402_1005Metric
R24, R25, R26, R27: R; R_0603_1608Metric; not fitted
R48: 220Ω; R_0402_1005Metric
TX4: XL-1608UBC-04; LED_0603_1608Metric
U2: MAX-M10S; ublox_MAX
U3: 74LVC1GU04; SOT-23-5
U13: LSM6DSO; LGA-14_3x2.5mm_P0.5mm_LayoutBorder3x4y; MPN LSM6DSOTR

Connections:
+3.3V: C1.2, C2.2, C3.2, C4.2, C5.2, C34.2, C35.2, C36.2, C37.1, C41.1, C42.1, E22-400M22S2.9 (VCC), IC1.1 (VDDIO), IC1.5 (SDO), IC1.6 (CSB), IC1.10 (VDD), R24.1, R25.1, R26.1, R27.1, U2.6 (V_BCKP), U2.7 (VCC_IO), U2.8 (VCC), U3.5 (VCC), U13.5 (VDDIO), U13.8 (VDD); also elsewhere on the board
/SENSORS/RXEN: E22-400M22S2.6 (RXEN), U3.4
/SENSORS/TXEN: E22-400M22S2.7 (TXEN), E22-400M22S2.8 (DIO2), U3.2
BMP_INT: IC1.7 (INT); also elsewhere on the board
BMP_SCL: IC1.2 (SCK), R25.2; also elsewhere on the board
BMP_SDA: IC1.4 (SDI), R24.2; also elsewhere on the board
GND: C1.1, C2.1, C3.1, C4.1, C5.1, C34.1, C35.1, C36.1, C37.2, C41.2, C42.2, D2.1 (A1), D5.1 (A1), E22-400M22S2.1 (GND), E22-400M22S2.2 (GND), E22-400M22S2.3 (GND), E22-400M22S2.4 (GND), E22-400M22S2.5 (GND), E22-400M22S2.10 (GND), E22-400M22S2.11 (GND), E22-400M22S2.12 (GND), E22-400M22S2.20 (GND), E22-400M22S2.22 (GND), IC1.3 (VSS_1), IC1.8 (VSS_2), IC1.9 (VSS_3), J1.2 (Ext), J12.2 (Ext), TX4.1 (K), U2.1 (GND), U2.10 (GND), U2.12 (GND), U2.15 (VIO_SEL), U3.3 (GND), U13.6 (GND@6), U13.7 (GND@7); also elsewhere on the board
GPS_RX: U2.3 (RXD); also elsewhere on the board
GPS_SCL: R27.2, U2.17 (SCL); also elsewhere on the board
GPS_SDA: R26.2, U2.16 (SDA); also elsewhere on the board
GPS_TX: U2.2 (TXD); also elsewhere on the board
IMU_CS: U13.12 (~CS); also elsewhere on the board
IMU_INT1: U13.4 (INT1); also elsewhere on the board
IMU_MISO: U13.1 (SDO/SA0); also elsewhere on the board
IMU_MOSI: U13.14 (SDA); also elsewhere on the board
IMU_SCK: U13.13 (SCL); also elsewhere on the board
LORA_CS: R4.1; also elsewhere on the board
LORA_DIO1: E22-400M22S2.13 (DIO1); also elsewhere on the board
LORA_IO0: E22-400M22S2.14 (BUSY); also elsewhere on the board
LORA_MISO: R1.1; also elsewhere on the board
LORA_MOSI: R2.1; also elsewhere on the board
LORA_NRST: E22-400M22S2.15 (NRST); also elsewhere on the board
LORA_SCK: R3.1; also elsewhere on the board
unnamed: D2.2 (A2), E22-400M22S2.21 (ANT), J1.1 (In)
unnamed: D5.2 (A2), J12.1 (In), U2.11 (RF_IN)
unnamed: E22-400M22S2.16 (MISO), R1.2
unnamed: E22-400M22S2.17 (MOSI), R2.2
unnamed: E22-400M22S2.19 (NSS), R4.2
unnamed: E22-400M22S2.18 (SCK), R3.2
unnamed: R48.1, TX4.2 (A)
unnamed: R48.2, U2.4 (TIMEPULSE)

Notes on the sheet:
GPS
IMU
LoRa
BARO

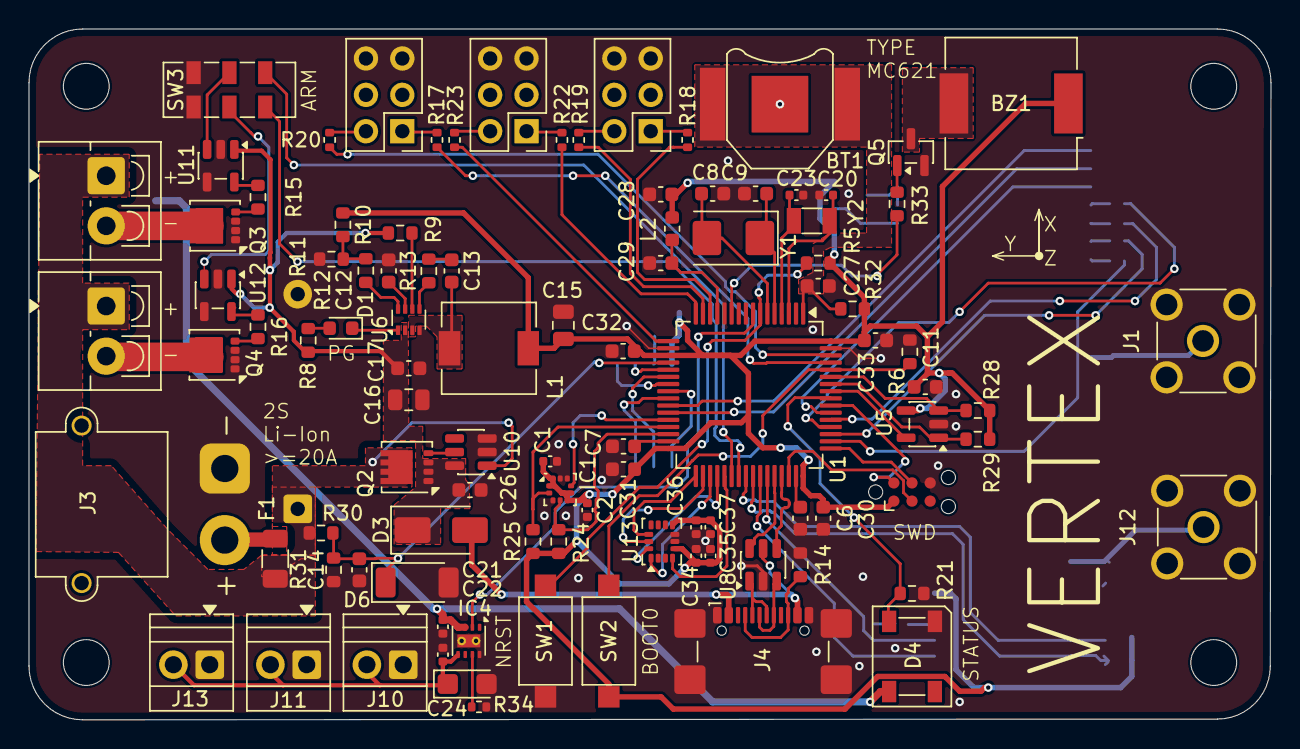
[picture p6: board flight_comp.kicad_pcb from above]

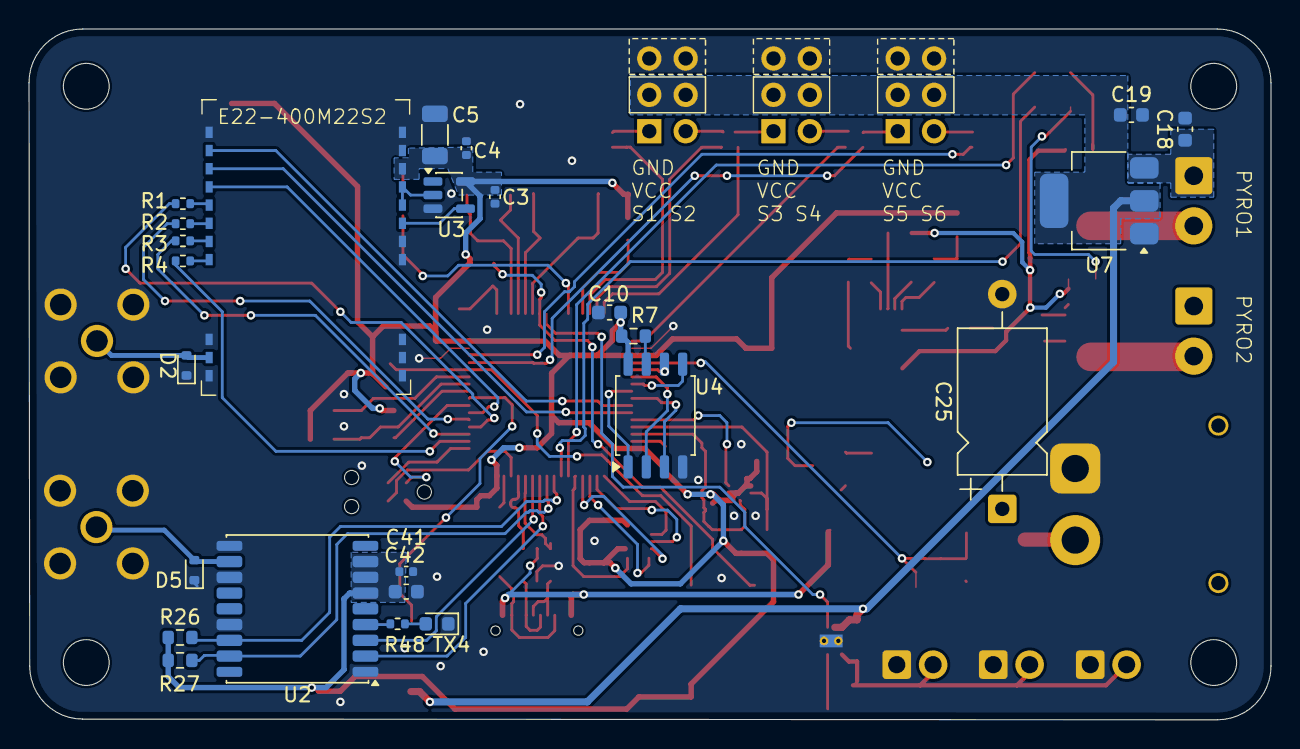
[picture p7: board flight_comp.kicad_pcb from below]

Board: 4 copper layers, 86.7 x 48.2 mm, 127 parts (25 on the bottom side), 103 nets.

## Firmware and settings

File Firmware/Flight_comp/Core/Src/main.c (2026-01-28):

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
/* Includes ------------------------------------------------------------------*/
#include "main.h"
#include "usb_device.h"

/* USER CODE BEGIN Includes */
#include "25flash.h"
#include "neopixel.h"
#include "buzzer.h"
#include "lsm6dso.h"
#include "BMP388.h"
#include "ee24.h"
#include "servo.h"
#include "GNSS.h"
#include "SX1262.h"
/* USER CODE END Includes */

/* USER CODE BEGIN PD */
#define VBAT_DIV_K  2.54

#define LSM6DSO_I2C_ADDR (0x6A << 1)
/* USER CODE END PD */

ADC_HandleTypeDef hadc1;

CRC_HandleTypeDef hcrc;

I2C_HandleTypeDef hi2c1;
I2C_HandleTypeDef hi2c2;
I2C_HandleTypeDef hi2c3;

RTC_HandleTypeDef hrtc;

SPI_HandleTypeDef hspi1;
SPI_HandleTypeDef hspi2;
SPI_HandleTypeDef hspi3;

TIM_HandleTypeDef htim3;
TIM_HandleTypeDef htim4;
TIM_HandleTypeDef htim5;
DMA_HandleTypeDef hdma_tim3_ch1_trig;

UART_HandleTypeDef huart1;

/* USER CODE BEGIN PV */
LSM6DSO_Object_t lsm6dso1;

float battery_v;
uint32_t adc_buff[1];
/* USER CODE END PV */

void SystemClock_Config(void);
static void MX_GPIO_Init(void);
static void MX_DMA_Init(void);
static void MX_ADC1_Init(void);
static void MX_I2C1_Init(void);
static void MX_I2C2_Init(void);
static void MX_I2C3_Init(void);
static void MX_RTC_Init(void);
static void MX_SPI1_Init(void);
static void MX_SPI2_Init(void);
static void MX_SPI3_Init(void);
static void MX_TIM3_Init(void);
static void MX_TIM4_Init(void);
static void MX_TIM5_Init(void);
static void MX_USART1_UART_Init(void);
static void MX_CRC_Init(void);
/**
  * @brief  The application entry point.
  * @retval int
  */
int main(void)
{

  /* MCU Configuration--------------------------------------------------------*/

  /* Reset of all peripherals, Initializes the Flash interface and the Systick. */
  HAL_Init();

  /* Configure the system clock */
  SystemClock_Config();

  /* Initialize all configured peripherals */
  MX_GPIO_Init();
  MX_DMA_Init();
  MX_ADC1_Init();
  MX_I2C1_Init();
  MX_I2C2_Init();
  MX_I2C3_Init();
  MX_RTC_Init();
  MX_SPI1_Init();
  MX_SPI2_Init();
  MX_SPI3_Init();
  MX_TIM3_Init();
  MX_TIM4_Init();
  MX_TIM5_Init();
  MX_USART1_UART_Init();
  MX_USB_DEVICE_Init();
  MX_CRC_Init();
  /* USER CODE BEGIN 2 */
  LSM6DSO_Init(&lsm6dso1);
  /* USER CODE END 2 */

  /* Infinite loop */
  /* USER CODE BEGIN WHILE */
  while (1)
  {
    /* USER CODE END WHILE */

    /* USER CODE BEGIN 3 */
  }
  /* USER CODE END 3 */
}

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
/* USER CODE BEGIN 4 */
void Get_Vbat(){
  HAL_ADC_Start_DMA(&hadc1, adc_buff, 1);
}

void HAL_ADC_ConvCpltCallback(ADC_HandleTypeDef *hadc)
{
  if(hadc->Instance == ADC1){
    battery_v = (adc_buff[1] * 3.3 / 4095)*VBAT_DIV_K;
  }
}


int32_t platform_write(void *handle, uint8_t reg, const uint8_t *bufp, uint16_t len)
{
    HAL_I2C_Mem_Write(handle,
                      LSM6DSO_I2C_ADDR,
                      reg,
                      I2C_MEMADD_SIZE_8BIT,
                      (uint8_t *)bufp,
                      len,
                      HAL_MAX_DELAY);
    return 0;
}

int32_t platform_read(void *handle, uint8_t reg, uint8_t *bufp, uint16_t len)
{
    HAL_I2C_Mem_Read(handle,
                     LSM6DSO_I2C_ADDR,
                     reg,
                     I2C_MEMADD_SIZE_8BIT,
                     bufp,
                     len,
                     HAL_MAX_DELAY);
    return 0;
}

void platform_delay(uint32_t ms)
{
    HAL_Delay(ms);
}
/* USER CODE END 4 */
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


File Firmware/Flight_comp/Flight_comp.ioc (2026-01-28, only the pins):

Mcu.UserName=STM32F405RGTx
PA0-WKUP.GPIO_Label=SERVO1
PA0-WKUP.Signal=S_TIM5_CH1
PA1.GPIO_Label=SERVO2
PA1.Signal=S_TIM5_CH2
PA10.GPIO_Label=GPS_RX
PA10.Signal=USART1_RX
PA11.Signal=USB_OTG_FS_DM
PA12.Signal=USB_OTG_FS_DP
PA13.Signal=SYS_JTMS-SWDIO
PA14.Signal=SYS_JTCK-SWCLK
PA15.GPIO_Label=LORA_NSS
PA15.Signal=SPI3_NSS
PA2.GPIO_Label=SERVO3
PA2.Signal=S_TIM5_CH3
PA3.GPIO_Label=SERVO4
PA3.Signal=S_TIM5_CH4
PA4.GPIO_Label=BAT_VSENCE
PA4.Signal=ADCx_IN4
PA5.GPIO_Label=FLASH_SCK
PA5.Signal=SPI1_SCK
PA6.GPIO_Label=FLASH_MISO
PA6.Signal=SPI1_MISO
PA7.GPIO_Label=FLASH_MOSI
PA7.Signal=SPI1_MOSI
PA8.GPIO_Label=GPS_SCL
PA8.Signal=I2C3_SCL
PA9.GPIO_Label=GPS_TX
PA9.Signal=USART1_TX
PB0.GPIO_Label=LORA_DIO1
PB0.Signal=GPIO_Output
PB1.GPIO_Label=LORA_IO0
PB1.Signal=GPIO_Input
PB10.GPIO_Label=BMP_SCL
PB10.Signal=I2C2_SCL
PB11.GPIO_Label=BMP_SDA
PB11.Signal=I2C2_SDA
PB12.GPIO_Label=IMU_NSS
PB12.Signal=SPI2_NSS
PB13.GPIO_Label=IMU_SCK
PB13.Signal=SPI2_SCK
PB14.GPIO_Label=IMU_MISO
PB14.Signal=SPI2_MISO
PB15.GPIO_Label=IMU_MOSI
PB15.Signal=SPI2_MOSI
PB2.GPIO_Label=BMP_INT
PB2.Signal=GPXTI2
PB3.Signal=SYS_JTDO-SWO
PB4.GPIO_Label=LED
PB4.Signal=S_TIM3_CH1
PB5.GPIO_Label=EEP_WP
PB5.Signal=GPIO_Output
PB6.GPIO_Label=EEP_SCL
PB6.Signal=I2C1_SCL
PB7.GPIO_Label=EEP_SDA
PB7.Signal=I2C1_SDA
PB8.GPIO_Label=SERVO5
PB8.Signal=S_TIM4_CH3
PB9.GPIO_Label=SERVO6
PB9.Signal=S_TIM4_CH4
PC0.GPIO_Label=CAM_CTRL
PC0.Signal=GPIO_Output
PC10.GPIO_Label=LORA_SCK
PC10.Signal=SPI3_SCK
PC11.GPIO_Label=LORA-MISO
PC11.Signal=SPI3_MISO
PC12.GPIO_Label=LORA_MOSI
PC12.Signal=SPI3_MOSI
PC14-OSC32_IN.Signal=RCC_OSC32_IN
PC15-OSC32_OUT.Signal=RCC_OSC32_OUT
PC3.GPIO_Label=BUZZER
PC3.Signal=GPIO_Output
PC4.GPIO_Label=FLASH_NSS
PC4.Signal=GPIO_Output
PC5.GPIO_Label=FLASH_WP
PC5.Signal=GPIO_Output
PC6.GPIO_Label=IMU_INT1
PC6.Signal=GPXTI6
PC7.GPIO_Label=PYRO1
PC7.Signal=GPIO_Output
PC8.GPIO_Label=PYRO2
PC8.Signal=GPIO_Output
PC9.GPIO_Label=GPS_SDA
PC9.Signal=I2C3_SDA
PD2.GPIO_Label=LORA_NRST
PD2.Signal=GPIO_Output
PH0-OSC_IN.Signal=RCC_OSC_IN
PH1-OSC_OUT.Signal=RCC_OSC_OUT

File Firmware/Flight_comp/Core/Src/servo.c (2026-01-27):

/*
 * servo.c
 *
 *		The MIT License.
 *  Created on: 01.08.2018
 *      Author: Mateusz Salamon
 *      www.msalamon.pl
 *		mateusz@msalamon.pl
 *
 *      Website: https://msalamon.pl/jak-pomachac-swoim-orczykiem-stm32-spotyka-sie-z-serwem/
 *      GitHub:  https://github.com/lamik/Servos_PWM_STM32_HAL
 */
#include "main.h"

#include "servo.h"

//
//	Servo innitialization
//
void Servo_Init(servo_t *servo, TIM_HandleTypeDef *_htim, uint32_t _channel)
{
	servo->htim = _htim;
	servo->channel = _channel;

	HAL_TIM_PWM_Start(servo->htim, servo->channel);
}

//
//	map help function
//
long map(long x, long in_min, long in_max, long out_min, long out_max)
{
  return (x - in_min) * (out_max - out_min) / (in_max - in_min) + out_min;
}

//
//	Servo set angle function
//
void Servo_SetAngle(servo_t *servo, uint16_t angle)
{
	if(angle < 0) angle = 0;
	if(angle > 180) angle = 180;

	  uint16_t tmp = map(angle, ANGLE_MIN, ANGLE_MAX, SERVO_MIN, SERVO_MAX);
	  __HAL_TIM_SET_COMPARE(servo->htim, servo->channel, tmp);
}

//
//	Servo set angle fine function
//
void Servo_SetAngleFine(servo_t *servo, float angle)
{
	if(angle < 0) angle = 0;
	if(angle > 180) angle = 180;

	  uint16_t tmp = map(angle, ANGLE_MIN, ANGLE_MAX, SERVO_MIN, SERVO_MAX);
	  __HAL_TIM_SET_COMPARE(servo->htim, servo->channel, tmp);
}

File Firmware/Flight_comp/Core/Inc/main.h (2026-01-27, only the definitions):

#define CAM_CTRL_Pin GPIO_PIN_0
#define CAM_CTRL_GPIO_Port GPIOC
#define BUZZER_Pin GPIO_PIN_3
#define BUZZER_GPIO_Port GPIOC
#define SERVO1_Pin GPIO_PIN_0
#define SERVO1_GPIO_Port GPIOA
#define SERVO2_Pin GPIO_PIN_1
#define SERVO2_GPIO_Port GPIOA
#define SERVO3_Pin GPIO_PIN_2
#define SERVO3_GPIO_Port GPIOA
#define SERVO4_Pin GPIO_PIN_3
#define SERVO4_GPIO_Port GPIOA
#define BAT_VSENCE_Pin GPIO_PIN_4
#define BAT_VSENCE_GPIO_Port GPIOA
#define FLASH_SCK_Pin GPIO_PIN_5
#define FLASH_SCK_GPIO_Port GPIOA
#define FLASH_MISO_Pin GPIO_PIN_6
#define FLASH_MISO_GPIO_Port GPIOA
#define FLASH_MOSI_Pin GPIO_PIN_7
#define FLASH_MOSI_GPIO_Port GPIOA
#define FLASH_NSS_Pin GPIO_PIN_4
#define FLASH_NSS_GPIO_Port GPIOC
#define FLASH_WP_Pin GPIO_PIN_5
#define FLASH_WP_GPIO_Port GPIOC
#define LORA_DIO1_Pin GPIO_PIN_0
#define LORA_DIO1_GPIO_Port GPIOB
#define LORA_IO0_Pin GPIO_PIN_1
#define LORA_IO0_GPIO_Port GPIOB
#define BMP_INT_Pin GPIO_PIN_2
#define BMP_INT_GPIO_Port GPIOB
#define BMP_SCL_Pin GPIO_PIN_10
#define BMP_SCL_GPIO_Port GPIOB
#define BMP_SDA_Pin GPIO_PIN_11
#define BMP_SDA_GPIO_Port GPIOB
#define IMU_NSS_Pin GPIO_PIN_12
#define IMU_NSS_GPIO_Port GPIOB
#define IMU_SCK_Pin GPIO_PIN_13
#define IMU_SCK_GPIO_Port GPIOB
#define IMU_MISO_Pin GPIO_PIN_14
#define IMU_MISO_GPIO_Port GPIOB
#define IMU_MOSI_Pin GPIO_PIN_15
#define IMU_MOSI_GPIO_Port GPIOB
#define IMU_INT1_Pin GPIO_PIN_6
#define IMU_INT1_GPIO_Port GPIOC
#define PYRO1_Pin GPIO_PIN_7
#define PYRO1_GPIO_Port GPIOC
#define PYRO2_Pin GPIO_PIN_8
#define PYRO2_GPIO_Port GPIOC
#define GPS_SDA_Pin GPIO_PIN_9
#define GPS_SDA_GPIO_Port GPIOC
#define GPS_SCL_Pin GPIO_PIN_8
#define GPS_SCL_GPIO_Port GPIOA
#define GPS_TX_Pin GPIO_PIN_9
#define GPS_TX_GPIO_Port GPIOA
#define GPS_RX_Pin GPIO_PIN_10
#define GPS_RX_GPIO_Port GPIOA
#define LORA_NSS_Pin GPIO_PIN_15
#define LORA_NSS_GPIO_Port GPIOA
#define LORA_SCK_Pin GPIO_PIN_10
#define LORA_SCK_GPIO_Port GPIOC
#define LORA_MISO_Pin GPIO_PIN_11
#define LORA_MISO_GPIO_Port GPIOC
#define LORA_MOSI_Pin GPIO_PIN_12
#define LORA_MOSI_GPIO_Port GPIOC
#define LORA_NRST_Pin GPIO_PIN_2
#define LORA_NRST_GPIO_Port GPIOD
#define LED_Pin GPIO_PIN_4
#define LED_GPIO_Port GPIOB
#define EEP_WP_Pin GPIO_PIN_5
#define EEP_WP_GPIO_Port GPIOB
#define EEP_SCL_Pin GPIO_PIN_6
#define EEP_SCL_GPIO_Port GPIOB
#define EEP_SDA_Pin GPIO_PIN_7
#define EEP_SDA_GPIO_Port GPIOB
#define SERVO5_Pin GPIO_PIN_8
#define SERVO5_GPIO_Port GPIOB
#define SERVO6_Pin GPIO_PIN_9
#define SERVO6_GPIO_Port GPIOB

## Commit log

2025-12-02 First commit. stm32 pin setup
    [flight_comp.kicad_pcb, flight_comp.kicad_sch]
2026-01-10 Production files
    [flight_comp-B_Cu.gbr, flight_comp-B_Mask.gbr, flight_comp-B_Paste.gbr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]
2026-01-27 EEP, IMU, BMP drivers, .ds_store removed
2026-01-27 Servo driver
2026-01-27 GNSS driver
2026-01-28 multiple build errors fixed
    [25flash.c, Flight_comp.ioc, main.c]

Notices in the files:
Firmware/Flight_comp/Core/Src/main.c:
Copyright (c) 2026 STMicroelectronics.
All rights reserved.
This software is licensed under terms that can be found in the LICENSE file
